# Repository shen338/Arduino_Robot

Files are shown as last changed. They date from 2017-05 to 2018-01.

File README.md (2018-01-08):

# Arduino Controlled Autonomous Robot for Ball Collection
In this project, we do the following things:  
· Employed Pixy Camera and image segmentation algorithm to locate the ball and container in real time  
· Wrote PID algorithm for the robot to track and follow the ball, programmed in Arduino IDE  
· Collaborated on the design and fabrication the robots powertrain, sensor and navigation hardware  

### Two demo ball tracking videos and our performance in final competition

[Final Competition](https://www.youtube.com/watch?v=fU1fNfBJTtA)   
[Ball Tracking Demo 1](https://www.youtube.com/watch?v=Wlfwm1OvA4c)  
[Ball Tracking Demo 2](https://www.youtube.com/watch?v=8-BpY_hJBjg)  

### Appearance of our robot: 
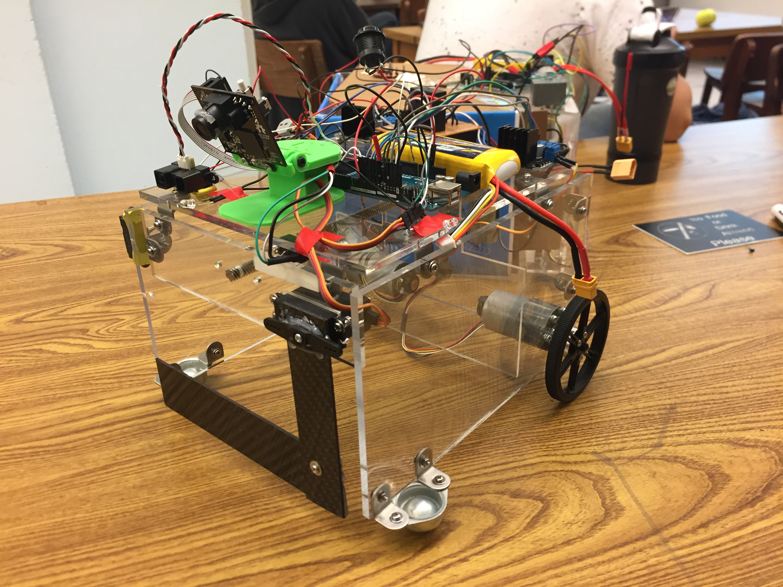
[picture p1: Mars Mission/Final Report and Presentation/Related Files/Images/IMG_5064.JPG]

### Appearance of our container: 
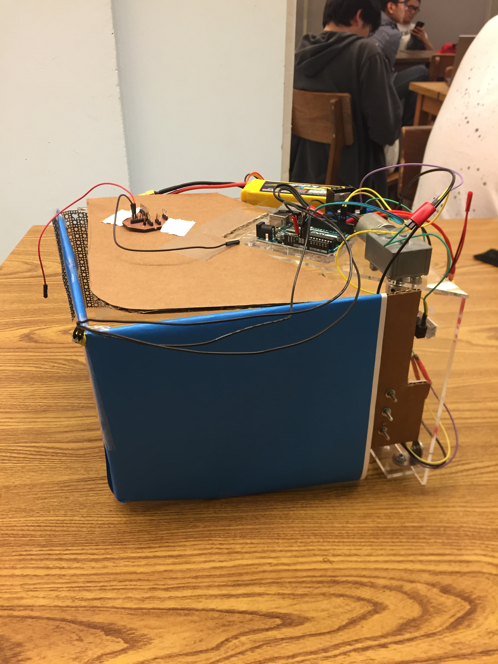
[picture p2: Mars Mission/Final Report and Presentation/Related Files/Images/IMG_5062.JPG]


#### All the source code is in the code/Master folder.

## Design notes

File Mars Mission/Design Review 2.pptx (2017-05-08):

## Design Review 2

Team 8
Ze An
Priyanka Anantha
De-Wei Chang
Andria Nyenhuis
Tong Shen

## FSM for the robot

Ball Tracking
TrackBlock(blocks,1);

size >= threshold

ball < 3

Ball Collecting
BallCollecting();

ball = 3

Ball Dispensing
BallPushing();

size >= threshold

Container Tracking
TrackBlock(blocks,2);

## FSM for ball dispensing

Forward
forward(255);

front switch = 0

Backward
backward(255);

rear switch = 0

Stop
backward(0);

## FSM for the container

Ball Tracking
TrackBlock(blocks,1);

size >= ?

ball < 3

Ball Collecting
BallCollecting();

ball = 3

Ball Dispensing
BallPushing();

Container Tracking
TrackBlock(blocks,2);

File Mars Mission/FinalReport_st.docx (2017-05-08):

1. ABSTRACT (Andria)
2. INTRODUCTION (Andria)
3. MECHANICAL SYSTEMS (Priyanka)
  3.1. Chassis and Component Mounts
  3.2. Trapdoor Mechanism
  3.3. Dispensing Mechanism
  3.4. Container
4. ELECTRONICS AND POWER SYSTEMS
  4.1. Microcontroller (De-Wei)

We used Arduino Mega 2560 as our controller on the robot because there are lots of pins on it to accommodate the pixy cam, three DC motors, a servo motor, two IR sensors, and infrared emitter. For the container, we use Arduino Uno as the controller due to just one DC motor and an infrared receiver.

  4.2. Actuators (De-Wei)
    4.2.1. Drive Motors

For the drive system, two 12V DC motors with encoders were used. These motor have no load speed of 251 rpm and 43.7:1 metal gearbox, which make it rotate fast and powerful. With L298N motor drive board, these motors can be easily controlled.

    4.2.2. Dispensing and Container Lead Screw Motor

For the lead screw driving motor, we used a 12V DC worm geared motor, which has huge torque to push heavy tennis balls. The only problem of this motor is that the rotational speed is not enough. Therefore, we couldn’t push the balls fast enough to have sufficient momentum to roll into the container by itself. As a result, we had no choice but to change the way we dispense the tennis balls.

    4.2.3. Trapdoor Motor

In order to easily control the door to be the specified positions, a servo motor was used to move the trapdoor. Moreover, there was no huge load on the door. Therefore, a servo motor was our best option.

  4.3. Sensors (Tong)
    4.3.1. Ball Detection

The ball detection mechanism is the core sensing part of our robot. Basically, we use the Pixy camera detection system to complete this part. First, we need to find the balls. To do this, we made our robot rotate itself if no ball was detected. And it also moved straight for a short distance in every 3 seconds to search in a different location. If a ball was detected, we need to detect the location of the ball as well as the distance between the ball and the vehicle. First, we need to know the relative position of the ball to navigate our vehicle. At very beginning, we used pan servo to rotate pixy to keep the ball in the center of the pixy camera and read the rotating angle of pan servo to compensate the move direction of our vehicle. In this way, we could successfully collect the ball but it was not fast enough and the precision and stability was not easy to control. So, we removed the pan servo and install the camera directly to our vehicle and read the relative position of the ball blocks in the image to compensate the moving direction of our vehicle. In this way, we could move our vehicle efficiently to the balls.

If the distance between the ball and the vehicle is small enough, we need to get into the collection state. First, we use the ball’s block size in the image to determine this distance. It turned out that the algorithm of the block size is unreliable in some corner cases. And then we found that y coordinate of the ball block in the image could also represent this distance. So, we changed our method and let the robot get into collection state after the ball block position in the image was low enough. In this way, we could make sure the vehicle would get into collection state every time at certain distance in front of the ball.

    4.3.2. Lead screw switches

To prevent the lead screw from moving beyond the limit to damage other components, we added to two switches in both side of the lead screw to regulate its moving range. Once the moving part touched the switch, it would stop or move to opposite direction immediately.

    4.3.3. Container Detection

It was easy to detect the container but the critical part was how to keep the alignment of the vehicle and the container to make sure the ball was dispensed in the right direction. We tested different method like the color code or mechanical structure guidance. But these method was not robust enough and couldn’t perfectly work in different situations. And then, we thought out of box and decided to change the shape of our container. We made a rectangle container and used a big color bar as a symbol. In this way, we didn’t need to worry about the vehicle direction in common cases. Our vehicle stopped in front of the container and got into dispensing state.

    4.3.4. Ultrasonic detection

In order to prevent our vehicle from hitting the wall, we introduced two ultrasonic sensor to our robot. In the searching mode, if any ultrasonic detected something, we could make some changes based on this information. We also developed an FSM for this to make sure our robot could go to the right way.

Task Completion - Container Door Close

For the door open and close, we used infrared signal as remote control to operate the container door. We installed three infrared emitter in the front and both sides of our robot and placed one receiver at the center of the container door. In this way, we could use our robot to open and close the container door.

  4.4. Power System
5. SOFTWARE (Ze An)
  5.1. Find Ball State
  5.2. Move to Ball State
  5.3. Obtain Ball State
  5.4. Dispense Ball State
  5.5. Container Close State
6. RESULTS
  6.1. Experiments and Testing
    6.1.1. Drive Motor Torque Testing (Ze)
    6.1.2. Ball Detection Testing (De Wei)

At the beginning, we used Pixy with pan and tilt servos mounted so that it can move as eyes on human's neck in order to get more vision. We first used the center point of the pixy camera to minus the x and y position of the block of the object to get the error, and use it to control the movement of the servo motors. After that, we took the angles the servos move from center as the error. With this error, we then built the differential speed for each sides of the motors to track the object. However, with feedback loop, it increased the difficulties to control the robot. As a result, we could successfully track tennis balls, but we failed to align with the balls perfectly. In other words, sometimes we might stop next to the ball, rather than in front of the ball, which made us unable to collect the ball. Therefore, we then tried to simplified the design and got rid of the pan and tilt servos, which sacrificed the broader range of vision. Without the servos for pan and tilt, we directly used the x axis error of pixy to build the differential speed for each motors. In this method, our robot would rotate without forward speed to search for the ball. Once aligned, it would go straight and collect it.

    6.1.3. Ball Collection Performance Testing (De Wei)

For the collection, we initially used size as the threshold to tell Arduino when to go into the collect state. However, after several tests, we found out that it was not stable as the size might vary with the light condition. Thus, we modified our method and used y position of the object as the threshold. We first used the serial monitor to find out the desired value as the robot approaching the tennis ball. After getting the desired value, we put it into the program and tested.

    6.1.4. Ball Dispensing Performance Testing (Andria)

The initial concept was to dispense the balls was to use a push plate driven by a lead screw mechanism. The plate however did not push the balls paste the plain of the vehicle. There were concerns that

    6.1.5. Container Door Performance Testing (Priyanka)
  6.2. Budget (Andria)
  6.3. Competition Performance (Andria)
7. DISCUSSION (Andria)
8. CONCLUSIONS (Andria)
9. REFERENCES
10. APPENDIX

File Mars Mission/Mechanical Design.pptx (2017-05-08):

## Mechanical Design

## Chasis

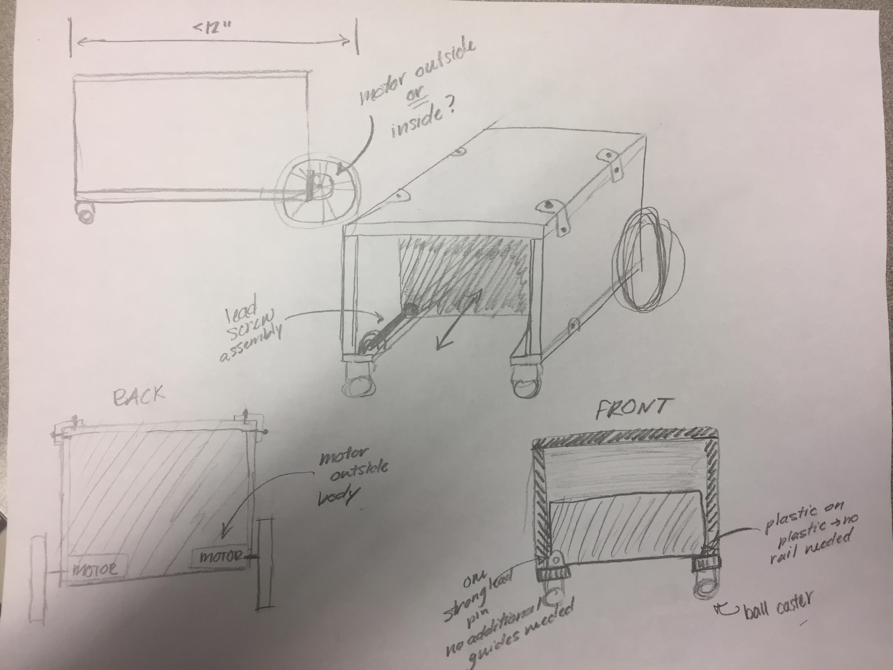
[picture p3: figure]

Andria’s concept

## BOM

ITEM | STATUS | LINK
Corner brackets | purchased | https://www.amazon.com/Tinksky-Stainless-Degree-Bracket-Fastener/dp/B01JOVO1N2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
M3 fasteners | purchased | https://www.amazon.com/290pcs-Phillips-Washers-Assortment-Stainless/dp/B01K6NNYZ8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
Lead screw assembly | purchased | https://www.amazon.com/Witbot-Pillow-Bearing-Coupler-Printer/dp/B01MXYIWTD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
3/4" Plastic Ball Caster | purchased | http://www.robotshop.com/en/pololu-ball-caster-3-4-in-plastic-ball.html

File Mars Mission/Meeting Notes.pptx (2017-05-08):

## Meeting Notes

Compiled

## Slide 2

Week | ACTIVITY 1 | ACTIVITY 2 | ACTIVITY 3 | ACTIVITY 4
2/27 | Prototype of body/chassis | Define motor req | Define container | Define sensor technology
3/6 | Define ball collector mechanism
3/13 (SPRING BREAK)
3/20 | Validate sensor technology
3/27
4/3 | 1st Design Critique
4/10
4/17 | 2nd Design Critique
4/24 | | | Report and Due day

## Meeting Notes

Friday, Feb 17

## Discussion

- Need to have rough idea of prototype by spring break to begin ordering parts
- Meet 2x a week until spring break
  - Tuesday 7 PM - weekly
  - Thursday 7 PM - weekly
  - Possibly additional meeting (March 3rd I think it was??)
- Image processing is slow
  - Not accurate
  - Not robust to different lighting
- Infrared could be a good option
- Ultra sonic would be difficult with walls reflecting
- possibly split team into subsystems : mechanical and electrical
- Corral the balls versus pick them up
- Compartment door could be passive by having it swivel on a hinge

## Product Attributes

- Robot
  - Drive motor/gears
  - Chassis
    - Wheels
    - Axles
  - Collecting system
    - Drive
    - Mechanism
  - Sensors
    - Detect wall
    - Detect ball
    - Detect compartment
  - Decorations
  - Body
  - Control board
  - Battery

- Compartment (12”x10”x6”)
  - Door (8”x6”)
    - Lift mechanism
    - Lift drive
      - Control board
      - Battery
  - Walls
  - Sensors
  - Decoration
    - Lighting
- Transportation Carrier (12”x12”x12”)

## Alumni Discussion

Feb 22, 2017

## Alumni meet discussions

Points noted:
- Options for sensing the balls:
  - IR sensors (noise and rangle problems)
  - Ultrasonic (noise problems)
  - Image sensors (pixy- compatible with raspberry pi, slow and takes more processing time but easier bot manipulation)
- To detect and align with container:
  - Hall effect sensor (short range distance)
  - Beacon (light emitting/wireless) (wireless-complicated)
- Use limit switches to detect collision with walls and helping in repositioning bot
- Can use encoders for position calculations but very tough to retrace steps
- Choose good friction tyres to avoid slip
- Brake/reverse motors if we want to push the balls out
- Design top loading container as it can be placed in any orientation

## Meeting Notes

Feb 23, 2017

## Discussion

- Container can be placed in any orientation in any corner therefore it might be necessary to drop balls in from the top or have doors on every side
  - Discussed how a claw armature would be easiest for dropping ball into the top of container
  - Discussed a possible container that raises from the middle so can be accessed from all sides, rubber band “arena” would keep balls from escaping from container
- Pixy (https://www.youtube.com/watch?v=MN-jYF7WYY4) discussed as a possible way of finding balls.. $70+$40
- 3 wheels for vehicle (2 drive, 1 caster)
- Motors : DC or Step
  - Have code for each

- Need to have a weekly 1.5 hour meeting set - Monday’s are preference since ordering days are Tuesday and Thursday
- Timeline
  - Before spring break
    - Define container
    - Rough prototype of vehicle
      - Motors
      - Ball carrying method
- To Do: Research motors *must order by 2/29
  - Possible option Nema 17 bipolar step motor 3.5V

## Meeting Notes

Feb 27, 2017

## Discussion

- Motor
  - Still trying to determine if DC or Step motor is the best solution - decided to test both - senior design lab has several different motors we could use if we have a driver
- Decided not to spend our time designing for balls in the corner, if there is time near the end of the project we can implement a method for getting balls that are in the corner
- RPM
  - Determined that 2.5m/3s (0.83m/s) is fast
    - With a 10 cm diameter wheel, vehicle RPM 158, motor RPM 5283.9
    - Motor rated 5000 step/s = 1500 RPM
- Wheels should be 10 cm

- Meet Thursday at 8 PM
  - Test motors
  - Andria to bring body prototype materials

## 1st Order Request (2/28)

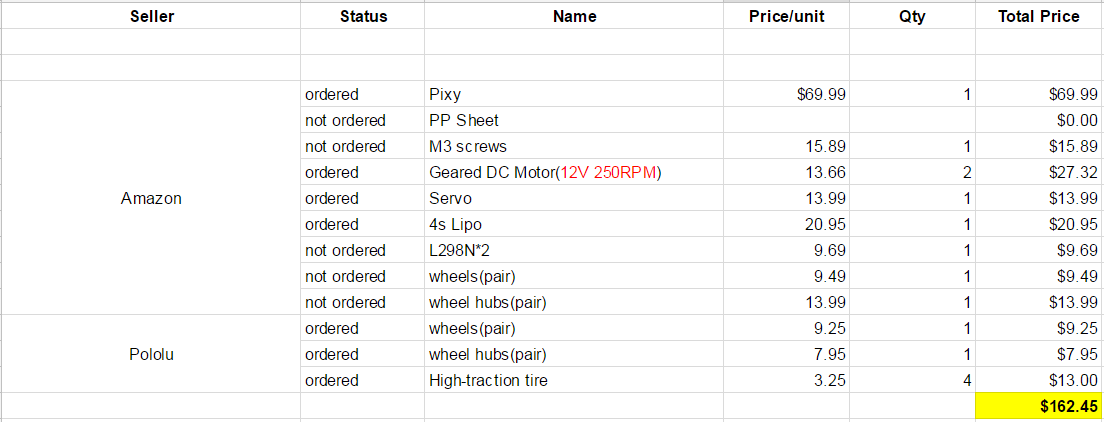
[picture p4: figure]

## Meeting Notes

March 2, 2017

## Discussion

- Andria’s friend asked prof/TA about balls being near the wall, they said they will not be placed near the wall.. They did not indicate the distance from the wall that would be considered “fair”
- Went through items we received for free from cabinets
  - See inventory sheet in folder
  - GB37Y3530-43 8EN DC Motor had great torque and RPM
  - Discussed if we should use the DC motors we order with worm gears or use GB37Y3530-43 8EN
- GB37Y3530-43 8EN would require the team to consider rear wheel drive and two front casters so that the front can remain open to capture balls - could keep motors in the front a create a “funnel” but we would be worried that the balls would reflect off of the funnel and not go through the funnel (see next slide for “funnel” concept
- Need to decide as a team if rear wheel drive would be okay? - this would require 2 front caster wheels.. Would casters mean too much start force? NEED TO DECIDE ASAP SO WE CAN ORDER!

- Built a container prototype
  - Decided it would be more simple to just have 2 doors (unless elastic band concept works)
    - Could use LED lights or color to lead robot to the correct door
  - Found that high ball force is required to push through the “flap” door
  - Considered strips of material.. Decided that would be a “curtain” not a door
  - May need to consider an axle type flap door so there is less force required to rotate (see next slide for axle flap door)
  - Did not try Ze’s elastic design but have elastic to try next time
  - Might need to consider a raising door if we can not get prototype to work

## Concepts

Front Wheel Drive Ball “Funnel”

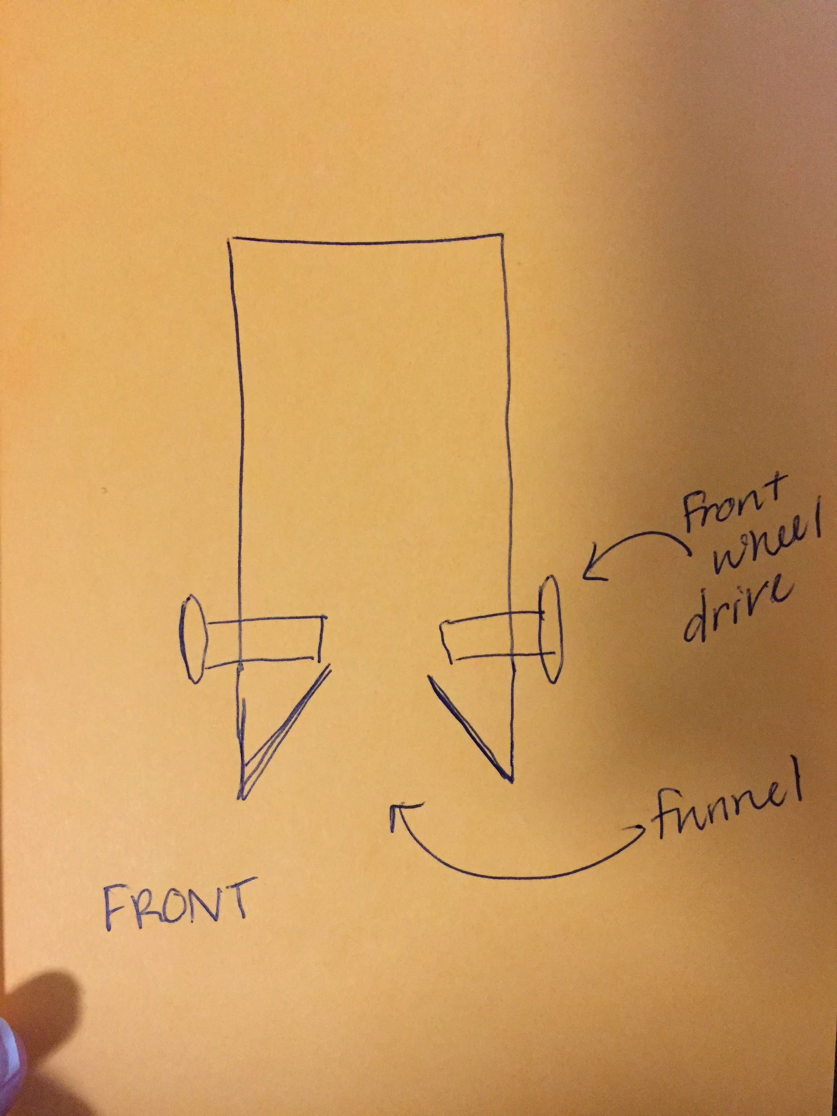
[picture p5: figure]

Axle Flap Door

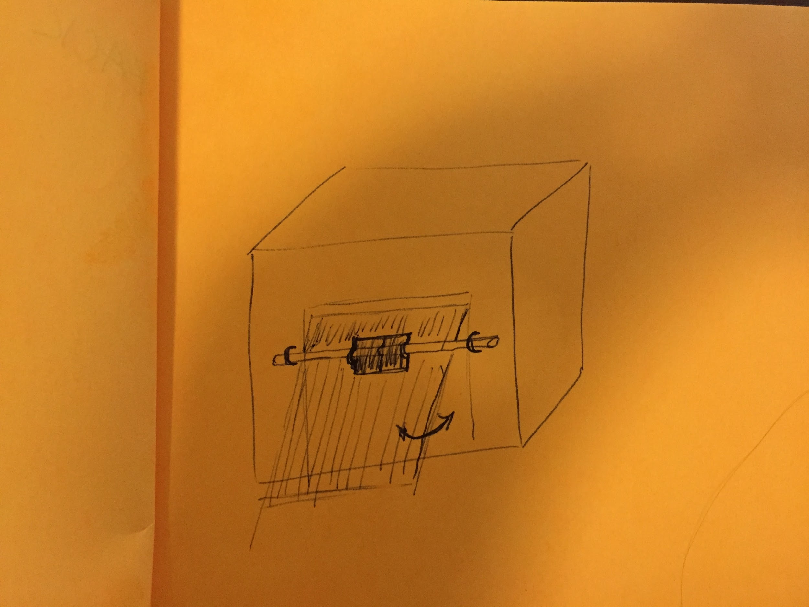
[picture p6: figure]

## Container Prototype

- Pros:
  - Easy to build
- Cons:
  - Requires a lot of force on the ball to push through doors

## Vehicle Prototype

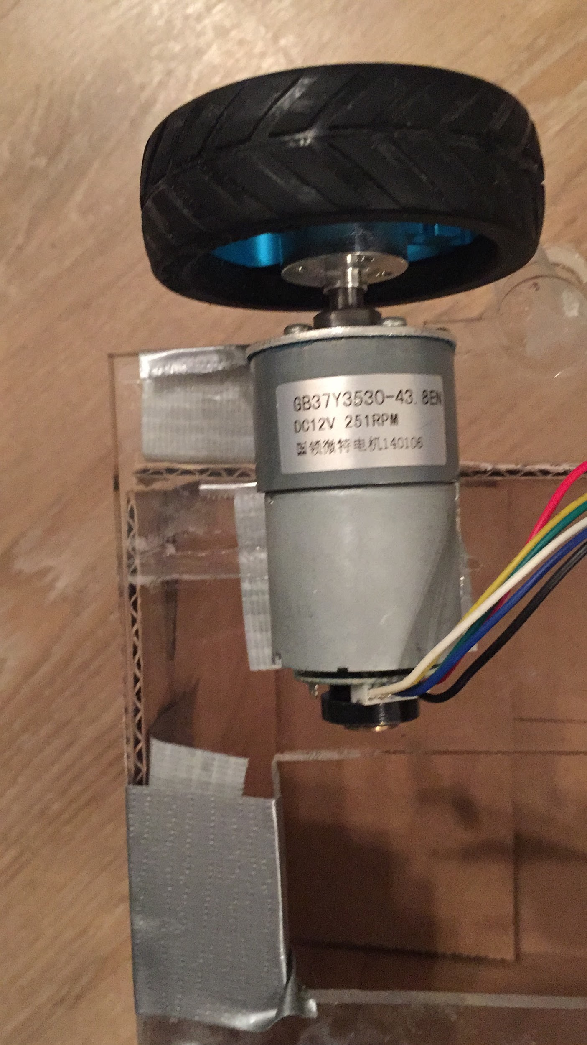
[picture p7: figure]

- 10”x7”x7”
- GB37Y3530-43 8EN
- 2.5” wheel

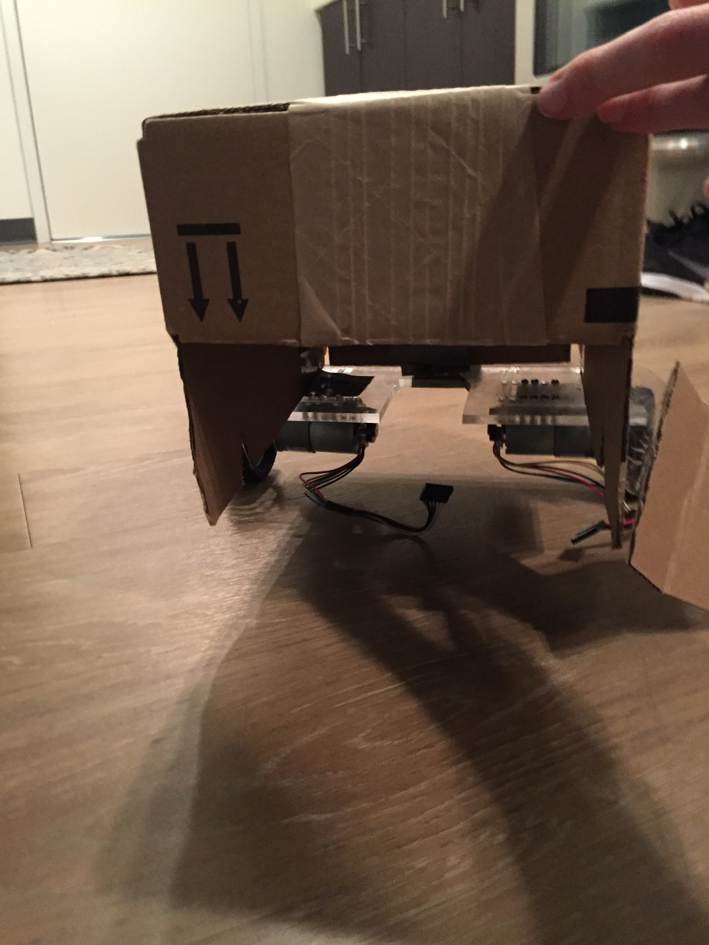
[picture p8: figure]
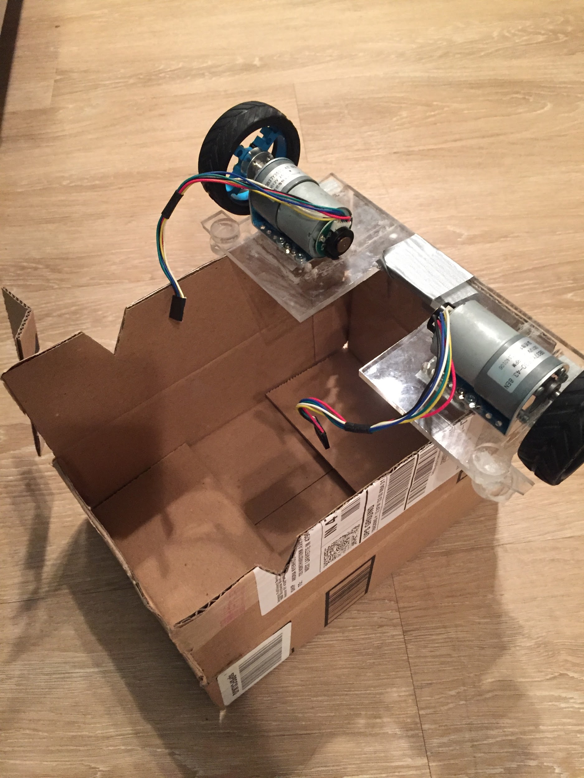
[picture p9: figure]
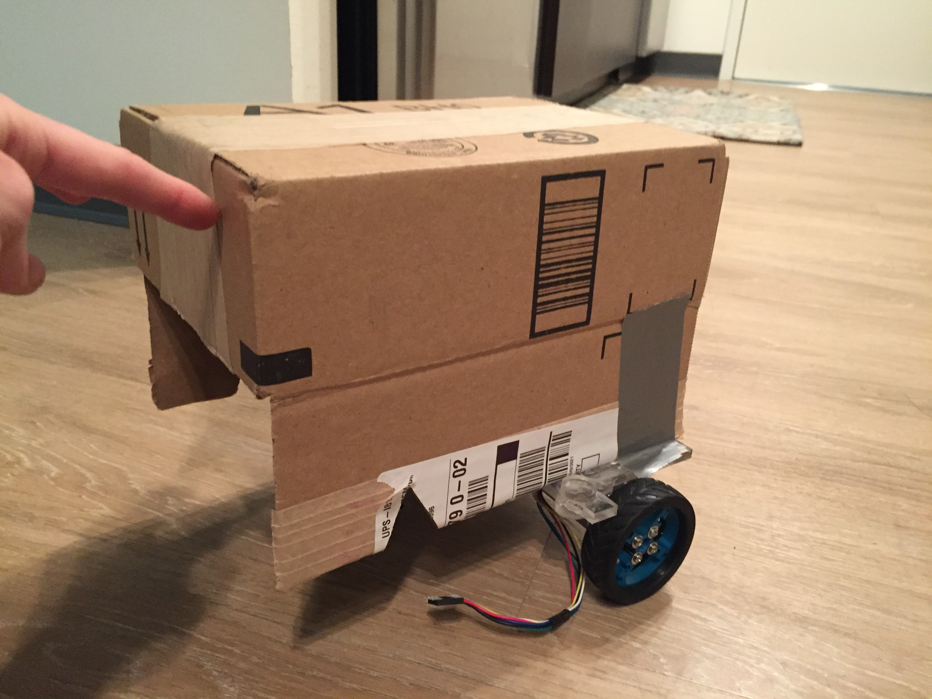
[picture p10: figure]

## Questions to ask in class

- Where to source our PCB through
- Door dimensions
- Door close time

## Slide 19

https://cdn-learn.adafruit.com/downloads/pdf/pixy-pet-robot-color-vision-follower-using-pixycam.pdf
https://create.arduino.cc/projecthub/junejarohan/ball-tracking-robot-7a9865
http://www.instructables.com/id/Pixybot-robots/?ALLSTEPS

## GitHub repository

https://github.com/MrBanana211/Mars_Mission

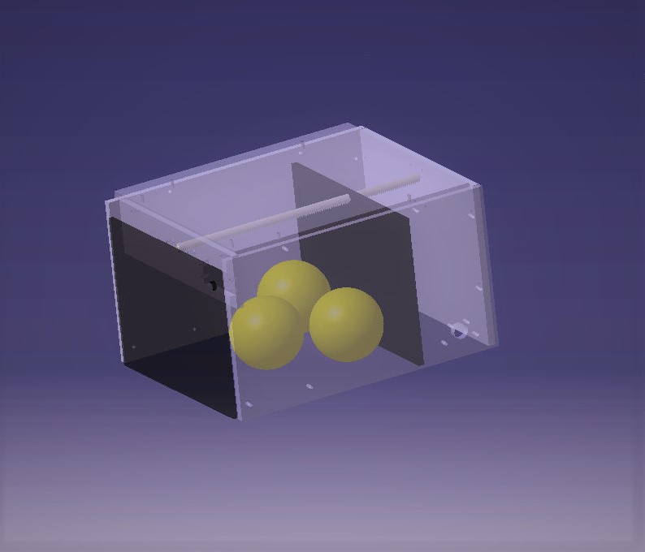
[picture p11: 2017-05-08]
Mars Mission/chassisdoor2.jpg

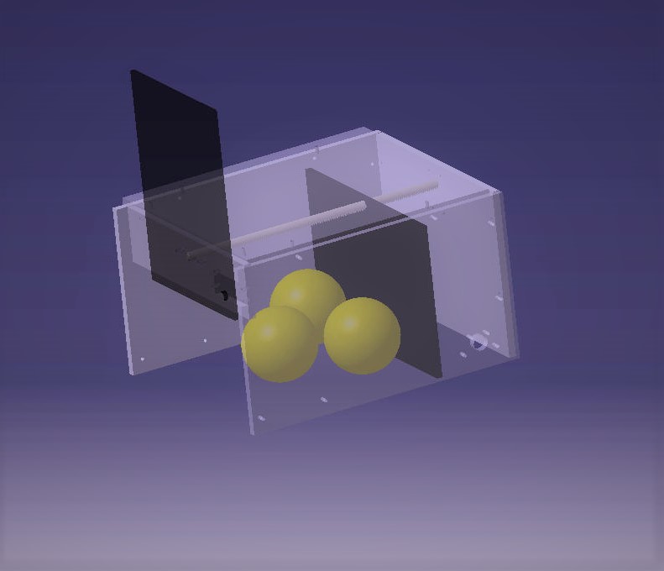
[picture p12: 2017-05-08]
Mars Mission/chassisdoor1.jpg

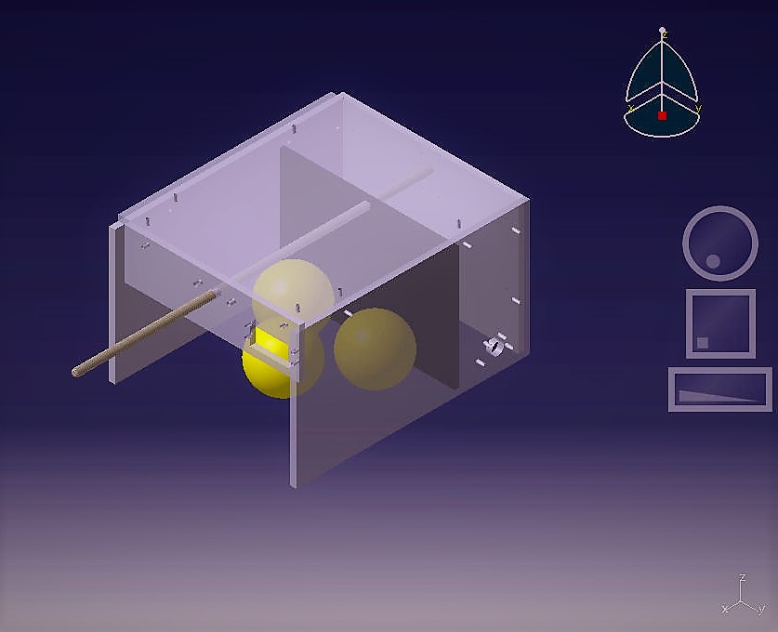
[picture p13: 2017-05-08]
Mars Mission/chassis1.jpg

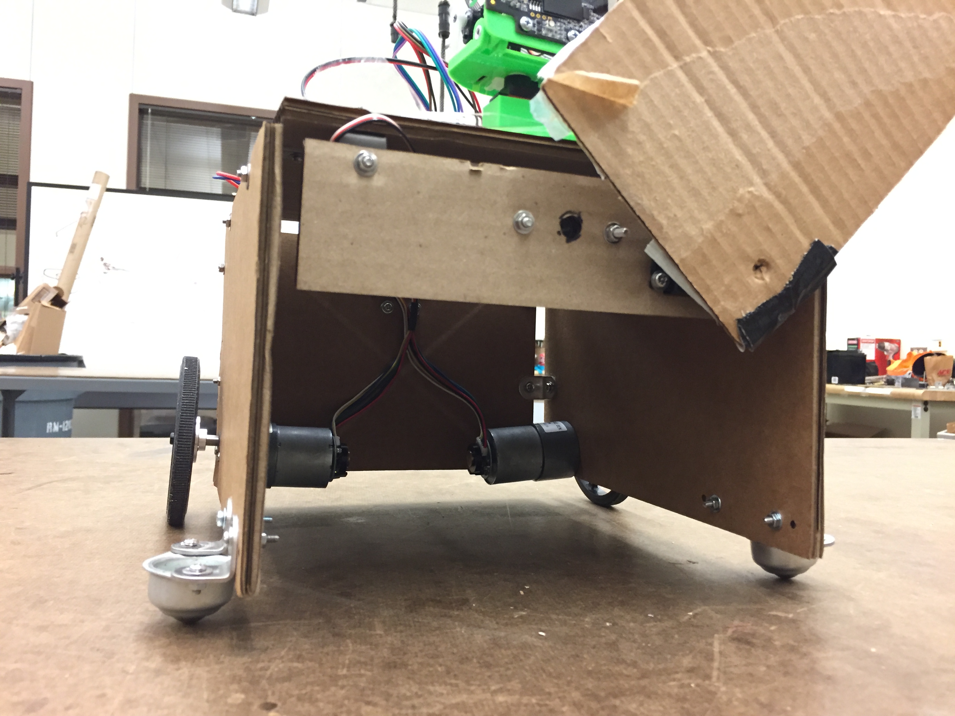
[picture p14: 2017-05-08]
Photos/2017-04-05 20.41.26.jpg

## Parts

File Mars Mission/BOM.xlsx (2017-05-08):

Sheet: Sheet1
Part Description | Subsystem | Vendor | Unit Price | Qty | Total Cost
Pixy Smart Vision | robot | amazon | 69.99 | 1 | 69.99
Geared DC Motor (12V 250 RPM) | robot/container | amazon | 13.66 | 2 | 27.32
Servo | robot | amazon | 13.99 | 1 | 13.99
wheels(pair) | robot | pololu | 9.25 | 1 | 9.25
wheel hubs (pair) | robot | pololu | 7.49 | 1 | 7.49
high traction tire | robot | pololu | 3.25 | 4 | 13
Ball Casters | robot | robot shop | 3.99 | 2 | 7.98
Witbot 400mm 8mm T8 Lead Screw Set | robot | amazon | 13.98 | 1 | 13.98
Corner Brackets | robot/container | amazon | 6.99 | 1 | 6.99
290pcs M3 Phillips Pan Head Fastener Assortment Kit | robot/container | amazon | 11.99 | 1 | 11.99
uxcell 6mm to 8mm Shaft Coupling | container | Amazon | 6.55 | 1 | 6.55
Hinge Roller Lever Micro Switches - 3 Pins 10 Pcs | robot/container | Amazon | 5.99 | 1 | 5.99
GB37Y3530-43 8EN | robot | on-hand | unknown | 2 | N/A
Arduino uno | container | on-hand | 24.95 | 1 | 24.95
Arduino Mega | robot | on-hand | 45.95 | 1 | 45.95
L298N | robot | on-hand | 3.23 | 3 | 9.69
ZIPPY Compact 1500mAh 3S 35C Lipo Pack | robot/container | on-hand | 14.34 | 2 | 28.68
Pixy servo | robot | on-hand | unknown | 1 | N/A
Pixy mount and servo | robot | on-hand | N/A | 1 | N/A
PCB | container | PCB Mill Shop | N/A | 1 | N/A
1/4" - 22"x18" arcylic sheet | robot | Menards | 19.94 | 1 | 19.94
1/8" - 22"x18" arcylic sheet | robot/container | on-hand | 16.48 | 1 | 16.48
5V voltage regualtor | robot | on-hand | unknown | 1 | N/A
Emergency switch | robot | on-hand | unknown | 1 | N/A
8 mm lead screw | container | on-hand | unknown | 1 | N/A
IR sensors (Qty:3) | robot/container | on-hand | unknown
LED (Qty 3) | robot | on-hand | unknown
carbon fiber scraps | robot | on-hand | unknown | 1 | N/A
TOTAL |  |  |  |  | 340.21

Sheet: Sheet2
Andria Out of Pocket Expenses
$25 | fasteners from Fastna
$40 | acrylic from menards (qty2)
$10 | L298N (Qty2)
$75 | SUM

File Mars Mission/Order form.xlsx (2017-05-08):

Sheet: Order 1
Seller | Status | Name | Price/unit | Qty | Total Price | Recieved status | Note | Link
Amazon | ordered | Pixy | $69.99 | 1 | $69.99 | Yes |  | https://www.amazon.com/Pixy-CMUcam5-Smart-Vision-Sensor/dp/B00IUYUA80
 | not ordered | PP Sheet |  |  | $0.00 |  | make cardboard prototype
 | not ordered | M3 screws | 15.89 | 1 | $15.89 |  |  | https://www.amazon.com/Hilitchi-210pcs-Stainless-Socket-Assortment/dp/B014ONCP88
 | ordered | Geared DC Motor(12V 250RPM) | 13.66 | 2 | $27.32 |  | Choose the one wiht Prime | https://www.amazon.com/dp/B01N990WOU/ref=olp_product_details?_encoding=UTF8&me=
 | ordered | Servo | 13.99 | 1 | $13.99 | Yes |  | https://www.amazon.com/Parallax-Inc-Continuous-Rotation-Servo/dp/B00B886KSE
 | ordered | 4s Lipo | 20.95 | 1 | $20.95 |  | 1300mAh | https://www.amazon.com/gp/product/B013I9RLVK/ref=ox_sc_act_title_2?ie=UTF8&psc=1&smid=A3T39NG71SCCQP
 | not ordered | L298N*2 | 9.69 | 1 | $9.69 |  |  | https://www.amazon.com/Stepper-Controller-Mega2560-Duemilanove-IFANCY-TECH/dp/B01GZ1QUHO?s=hi
 | not ordered | wheels(pair) | 9.49 | 1 | $9.49 |  | If possible buy from Pololu | https://www.amazon.com/gp/product/B00T3MQEU6/ref=ox_sc_act_title_1?ie=UTF8&psc=1&smid=A2XU70B31JRNMP
 | not ordered | wheel hubs(pair) | 13.99 | 1 | $13.99 |  | If possible buy from Pololu | https://www.amazon.com/Pololu-UNIVERSAL-ALUMINUM-MOUNTING-SHAFT/dp/B00B887FX8
Pololu | ordered | wheels(pair) | 9.25 | 1 | $9.25 | Yes |  | https://www.pololu.com/product/1431
 | ordered | wheel hubs(pair) | 7.95 | 1 | $7.95 | No |  | https://www.pololu.com/product/1083
 | ordered | High-traction tire | 3.25 | 4 | $13.00 | Yes | We definitely want these | https://www.pololu.com/product/694
 |  |  |  |  | $162.45

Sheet: Order 3
Seller | Name | Price/unit | Quantity | Total price | Link
Amazon | 6 mm to 8mm Helical Coupler | 6.99 | 1 | 6.99 | https://www.amazon.com/uxcell-5mmx8mm-Helical-Coupler-Coupling/dp/B06X99P2XK
 | uxcell 2 Pcs KFL08 8mm Zinc-Aluminum Alloy Flange Pillow Block Bearing | 9.15 | 1 | 9.15 | https://www.amazon.com/uxcell-Zinc-Aluminum-Flange-Pillow-Bearing/dp/B00N4138LU
 | uxcell 6mm to 8mm Shaft Coupling 25mm Length 18mm Diameter Stepper Motor Coupler Aluminum Alloy Joint Connector for 3D Printer CNC Machine DIY Encoder

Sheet: Order 2
Name | Price/unit | Quantity | Total price | Link
Pololu Ball Caster with 3/4" Plastic Ball | 3.99 | 2 | 7.98 | http://www.robotshop.com/en/pololu-ball-caster-3-4-in-plastic-ball.html
Witbot 400mm 8mm T8 Lead Screw Set Lead Screw+ Pillow Bearing Block + Copper Nut + Coupler for 3D Printer | 13.98 | 1 | 13.98 | https://www.amazon.com/Witbot-Pillow-Bearing-Coupler-Printer/dp/B01MXYIWTD
corner brackets | 6.99 | 1 | 6.99 | https://www.amazon.com/Tinksky-Stainless-Degree-Bracket-Fastener/dp/B01JOVO1N2?rps=1
290pcs M3 Phillips Pan Head Screws Bolts Nuts Lock Flat Washers Assortment Kit (M3,304 Stainless Steel) | 11.99 | 1 | 11.99 | https://www.amazon.com/290pcs-Phillips-Washers-Assortment-Stainless/dp/B01K6NNYZ8
 |  |  | 40.94
 | all received in Order 2

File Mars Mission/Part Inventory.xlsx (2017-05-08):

Description | Model Number | Picture | Notes
2 DC motors with 2.5" wheels | GB37Y3530-43 8EN |  | with encoders, and mounting base | https://www.dfrobot.com/wiki/index.php/12V_DC_Motor_251rpm_w/Encoder_(SKU:_FIT0186)
elastic band
variety of resistors
four bar link mechanism
2 Arduino Mega's |  |  | not sure if they work
2 heavy duty 2.5" casters
2 stepper motors with 2.75" wheels | 42BYGHM809
2 DC motors 3.5" wheels | LT25GA75-370T |  | 6V, 155+/- PRM, 1:75 gear ratio
gears and fasteners
11.1V 5000mAh 3-cell LiPo battery | TP5000-3sPP65
2* 2.5KG Electromagnet DC 12V P20/15 Holding Electric Magnet Lifting Solenoid |  |  | http://www.ebay.com/itm/like/162408602021?lpid=82&chn=ps&ul_noapp=true
breadboard
3* ultrasonic sensor | HC-SR04
2* bluetooth module
fuse
Dual MC33926 Motor Driver Carrier |  |  | https://www.pololu.com/product/1213
AC/DC power supply | LM2577 |  | https://www.amazon.com/Universal-adjustable-Module-Regulator-Booster/dp/B0043BHBR2
2* OP Amp | LM741
2* 8-bit ADC | ADC0809CCN |  | http://www.ti.com/lit/ds/symlink/adc0809-n.pdf
ISD 1420P

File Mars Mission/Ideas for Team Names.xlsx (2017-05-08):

Name | Reference
Ares | greek god of war

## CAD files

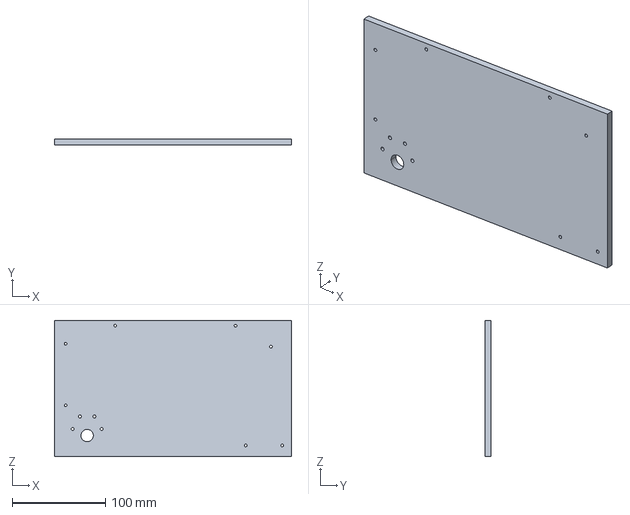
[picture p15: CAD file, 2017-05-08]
Mars Mission/Final Report and Presentation/Related Files/CAD Files/STP parts_chassis/sidewall.stp
254.0 x 6.35 x 146.1 mm

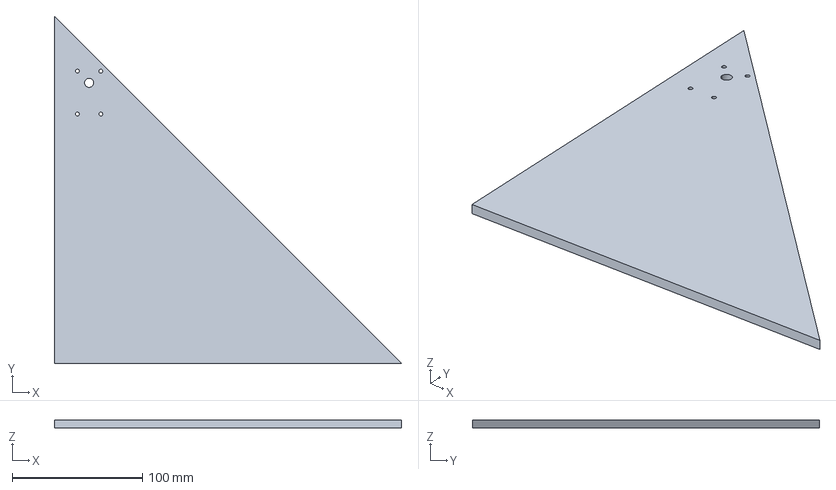
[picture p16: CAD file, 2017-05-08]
Mars Mission/Final Report and Presentation/Related Files/CAD Files/STP parts_container/top.stp
266.7 x 266.7 x 6.35 mm

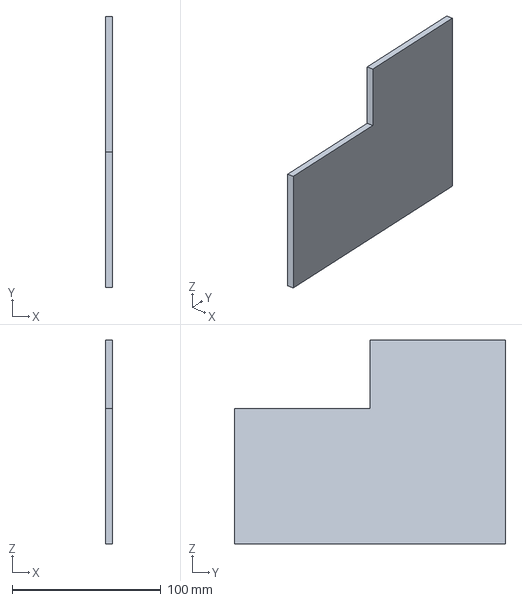
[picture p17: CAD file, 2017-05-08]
Mars Mission/Final Report and Presentation/Related Files/CAD Files/STP parts_chassis/door1.stp
5.00 x 182.5 x 137.1 mm

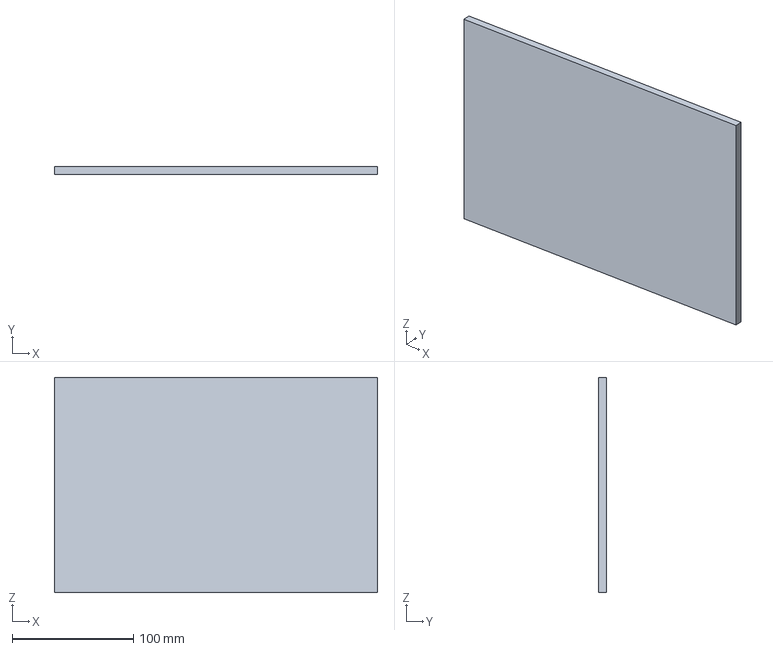
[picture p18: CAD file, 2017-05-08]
Mars Mission/Final Report and Presentation/Related Files/CAD Files/STP parts_container/c_wall.stp
266.7 x 6.35 x 177.8 mm

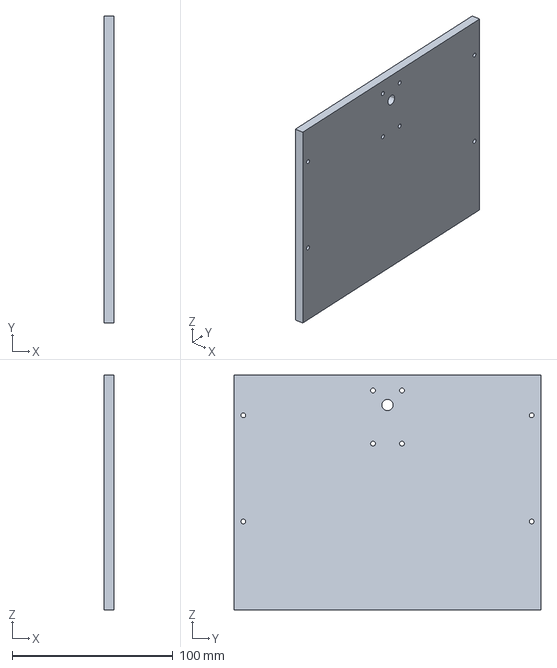
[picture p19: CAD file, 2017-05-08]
Mars Mission/Final Report and Presentation/Related Files/CAD Files/STP parts_chassis/backwall.stp
6.35 x 190.5 x 146.1 mm

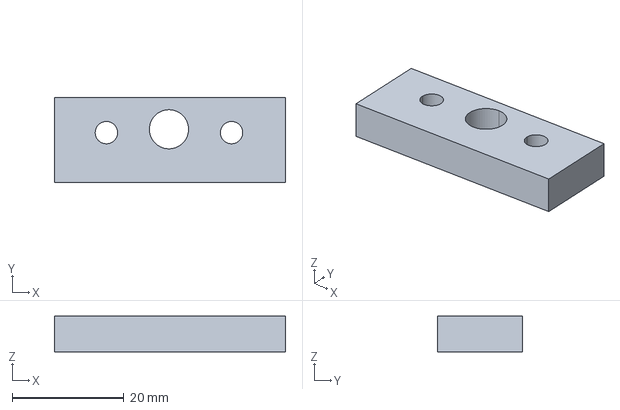
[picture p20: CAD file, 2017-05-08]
Mars Mission/Final Report and Presentation/Related Files/CAD Files/STP parts_container/support.stp
41.3 x 15.2 x 6.35 mm

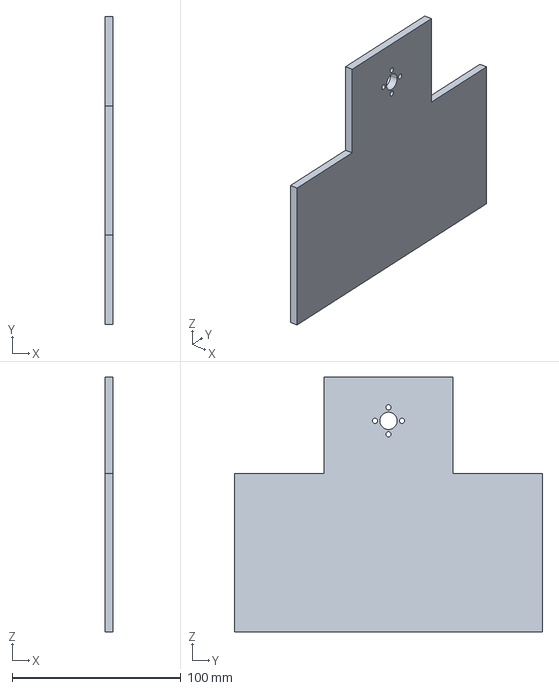
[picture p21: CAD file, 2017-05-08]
Mars Mission/Final Report and Presentation/Related Files/CAD Files/STP parts_chassis/plate.stp
5.00 x 183.0 x 151.3 mm

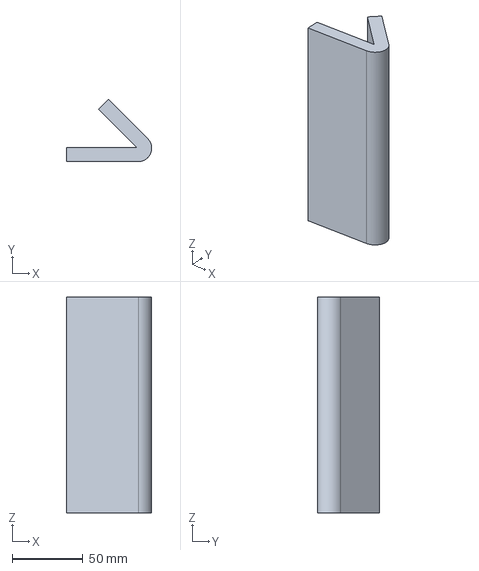
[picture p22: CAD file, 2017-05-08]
Mars Mission/Final Report and Presentation/Related Files/CAD Files/STP parts_container/guide.stp
60.3 x 44.0 x 152.4 mm

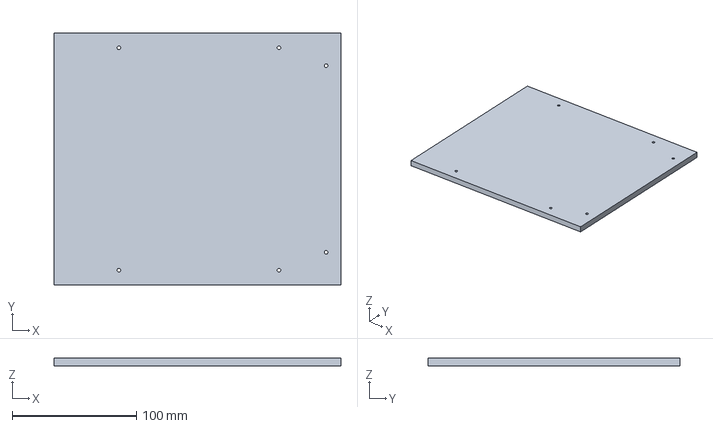
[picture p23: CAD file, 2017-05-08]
Mars Mission/Final Report and Presentation/Related Files/CAD Files/STP parts_chassis/topwall.stp
231.3 x 203.2 x 6.35 mm

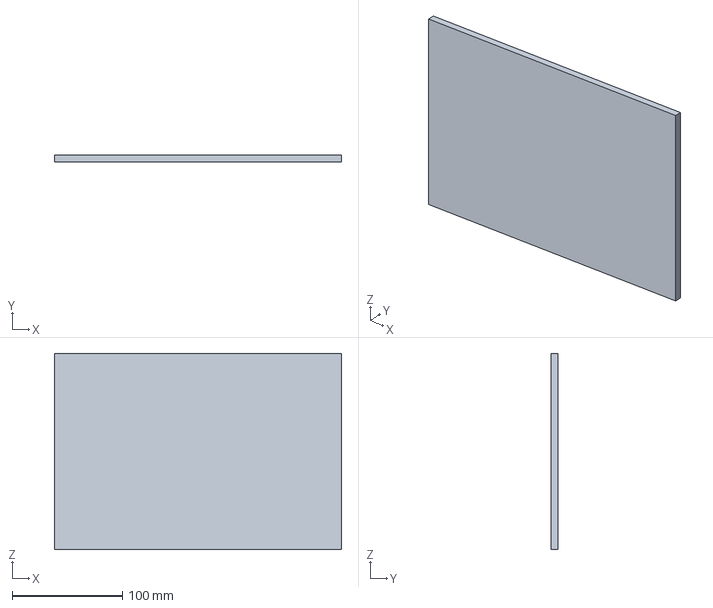
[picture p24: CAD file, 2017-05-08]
Mars Mission/Final Report and Presentation/Related Files/CAD Files/STP parts_container/c_wall2.stp
260.4 x 6.35 x 177.8 mm

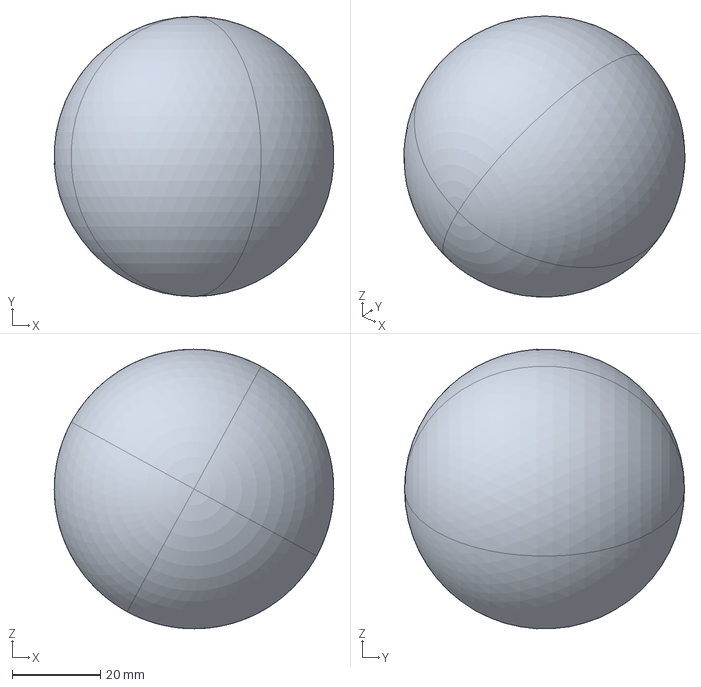
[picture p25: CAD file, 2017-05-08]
Mars Mission/Final Report and Presentation/Related Files/CAD Files/STP parts_chassis/balls.stp
63.4 x 63.5 x 63.4 mm

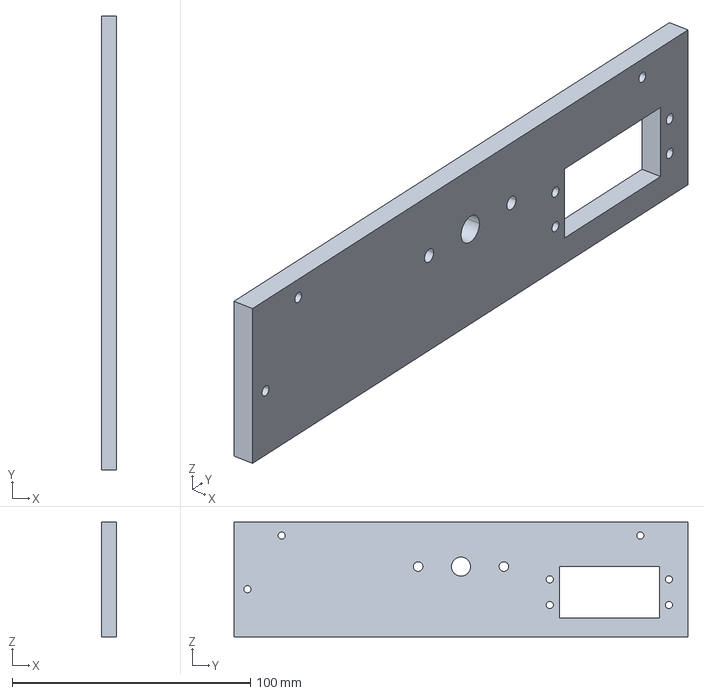
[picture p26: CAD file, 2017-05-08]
Mars Mission/Final Report and Presentation/Related Files/CAD Files/STP parts_chassis/frontwall.stp
6.35 x 190.5 x 48.2 mm

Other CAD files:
Mars Mission/Final Report and Presentation/Related Files/CAD Files/chassis2.dwg
Mars Mission/Final Report and Presentation/Related Files/CAD Files/Drawing1.dwg

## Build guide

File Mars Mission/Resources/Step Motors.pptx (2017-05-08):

## Step Motors

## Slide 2

https://www.youtube.com/watch?v=bkqoKWP4Oy4
http://www.servomagazine.com/index.php/magazine/article/september2014_Wierenga

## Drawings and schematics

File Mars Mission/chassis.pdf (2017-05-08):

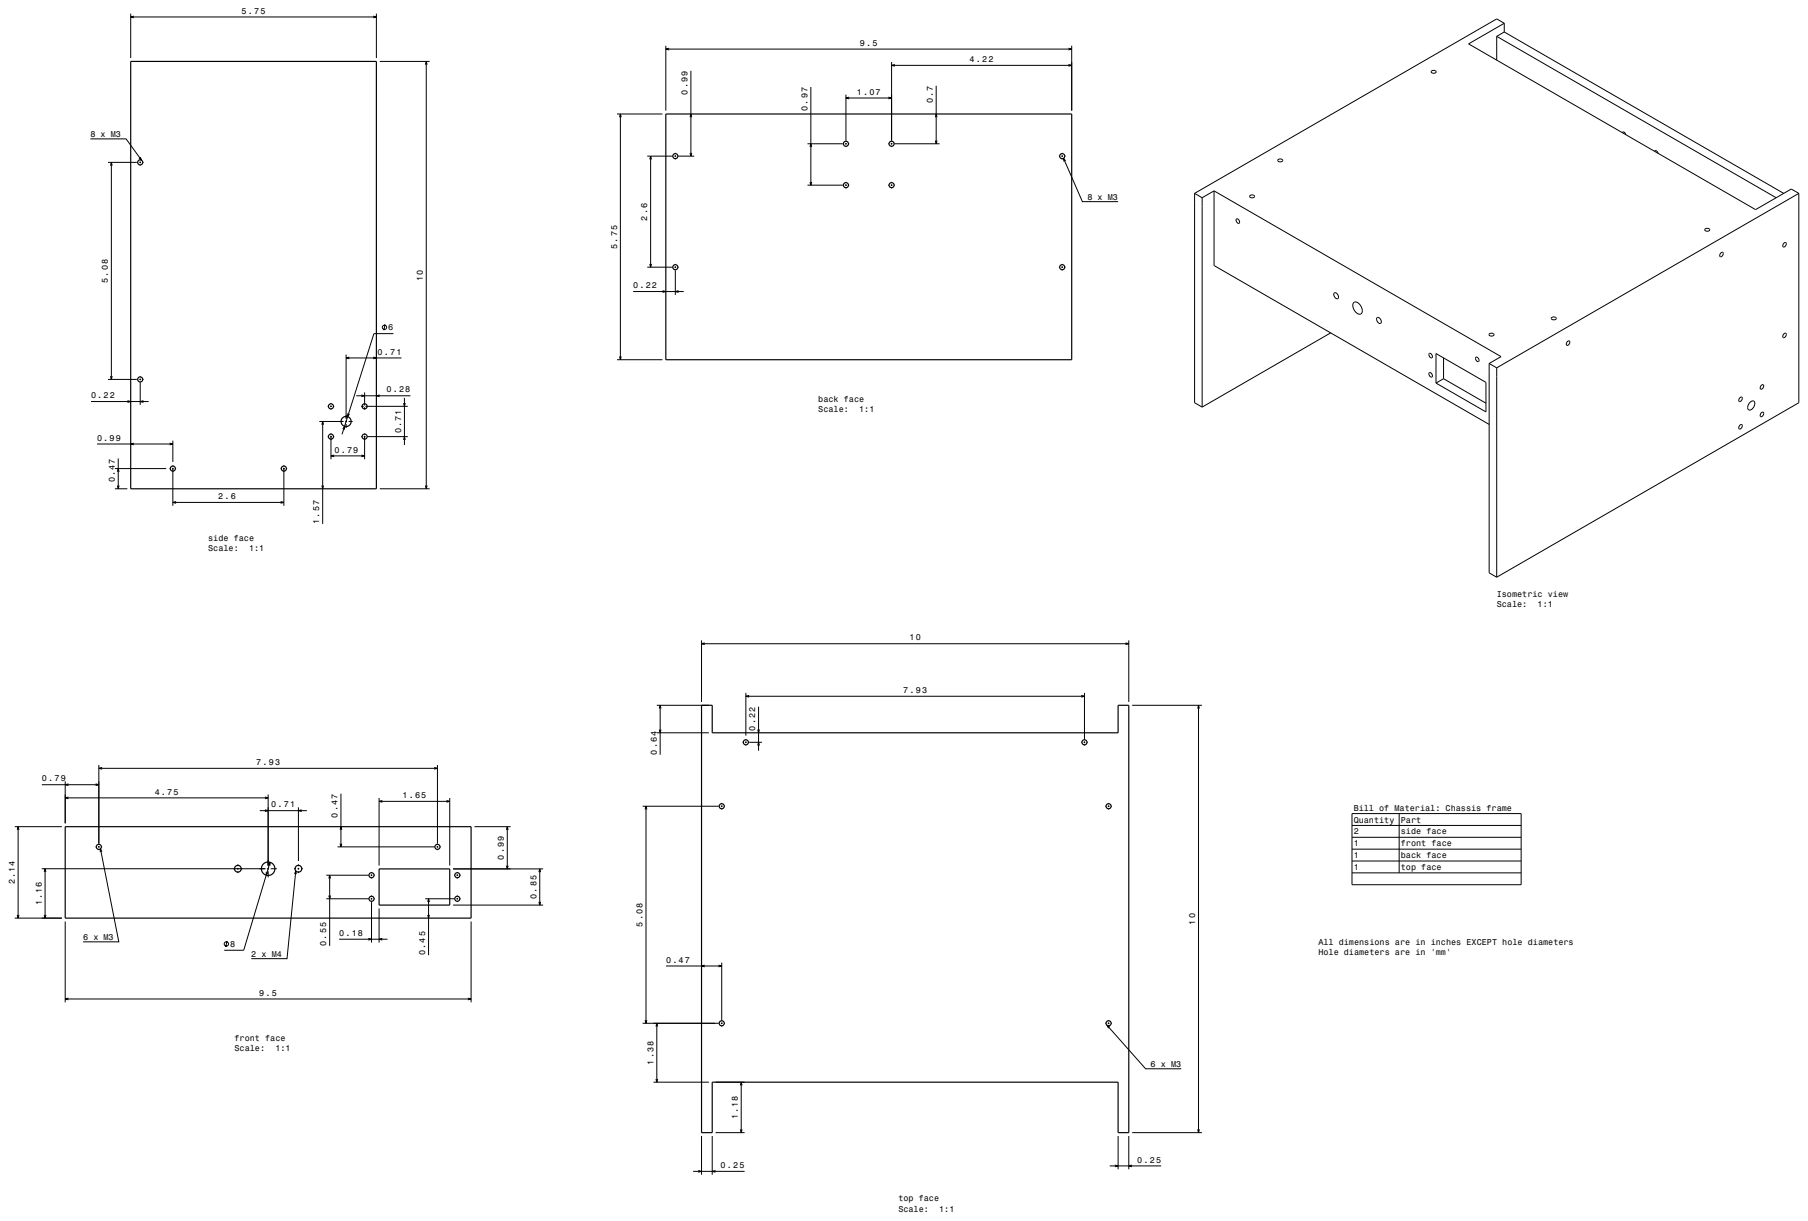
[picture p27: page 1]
side face Scale: 1:1; back face Scale: 1:1; top face Scale: 1:1; front face Scale: 1:1; Isometric view Scale: 1:1

Bill of Material: Chassis frame

Quantity | Part
2 | side face
1 | front face
1 | back face
1 | top face

All dimensions are in inches EXCEPT hole diameters
Hole diameters are in 'mm'

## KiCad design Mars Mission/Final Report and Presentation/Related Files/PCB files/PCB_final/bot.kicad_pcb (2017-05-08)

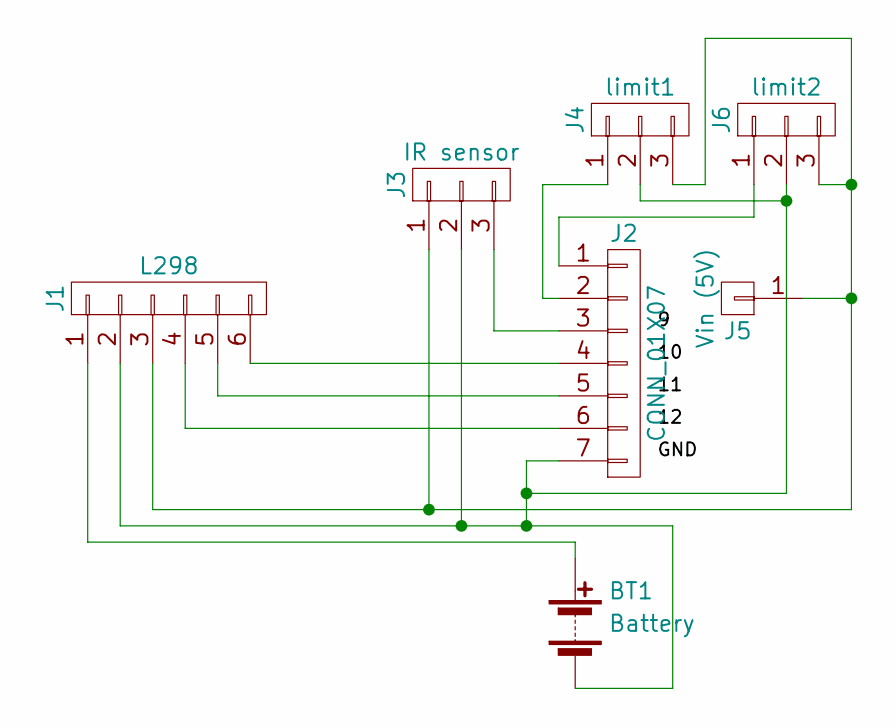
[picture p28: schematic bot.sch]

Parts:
BT1: Battery; Pin_Header_Straight_2x01_Pitch2.54mm
J1: L298; Pin_Header_Straight_1x06_Pitch2.54mm
J2: CONN_01X07; Pin_Header_Straight_1x07_Pitch2.54mm
J3: IR sensor; Pin_Header_Straight_1x03_Pitch2.54mm
J4: limit1; Pin_Header_Straight_1x03_Pitch2.54mm
J5: Vin (5V); Pin_Header_Straight_1x01_Pitch2.54mm
J6: limit2; Pin_Header_Straight_1x03_Pitch2.54mm

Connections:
unnamed: BT1.1 (+), J1.1
unnamed: BT1.2 (-), J1.2, J2.7, J3.2, J4.2, J6.2
unnamed: J1.3, J3.1, J4.3, J5.1, J6.3
unnamed: J1.4, J2.6
unnamed: J1.5, J2.5
unnamed: J1.6, J2.4
unnamed: J2.1, J6.1
unnamed: J2.2, J4.1
unnamed: J2.3, J3.3

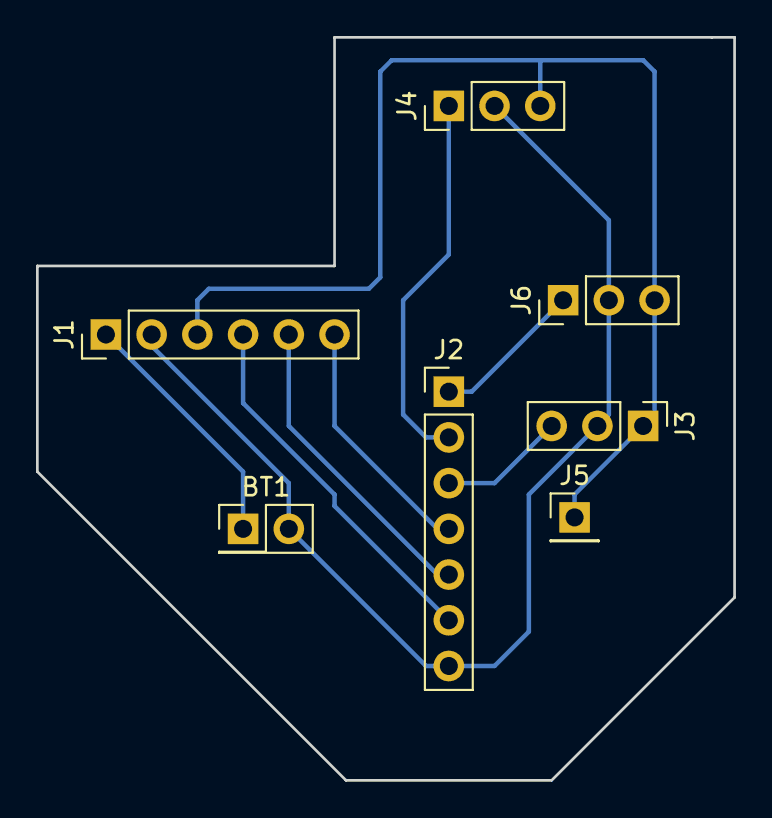
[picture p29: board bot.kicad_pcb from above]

Board: 2 copper layers, 38.7 x 41.3 mm, 7 parts (0 on the bottom side), 9 nets.

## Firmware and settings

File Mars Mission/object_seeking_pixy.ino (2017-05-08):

#include <SPI.h>
#include <Pixy.h>
//#include <ZumoMotors.h>
#define X_CENTER 160L
#define Y_CENTER 100L
#define RCS_MIN_POS 0L
#define RCS_MAX_POS 1000L
#define RCS_CENTER_POS ((RCS_MAX_POS-RCS_MIN_POS)/2)

const int motorL1 = 7;
const int motorL2 = 8;
const int motorLPWM = 6;

const int motorR1 = 12;
const int motorR2 = 13;
const int motorRPWM = 11;

//---------------------------------------
// Servo Loop Class
// A Proportional/Derivative feedback loop for pan/tilt servo tracking of blocks.
// (Based on Pixy CMUcam5 example code) //---------------------------------------
class ServoLoop
{ public:
ServoLoop(int32_t proportionalGain, int32_t derivativeGain);
void update(int32_t error);
int32_t m_pos;
int32_t m_prevError; 
int32_t m_proportionalGain; 
int32_t m_derivativeGain;
};

// ServoLoop Constructor
ServoLoop::ServoLoop(int32_t proportionalGain, int32_t derivativeGain) {
m_pos = RCS_CENTER_POS;
m_proportionalGain = proportionalGain;
m_derivativeGain = derivativeGain; 
m_prevError = 0x80000000L;
}
// ServoLoop Update
// Calculates new output based on the measured error and the current state.
void ServoLoop::update(int32_t error)
{
long int velocity;
char buf[32];
if (m_prevError!=0x80000000) {
  velocity = (error*m_proportionalGain + (error - m_prevError)*m_derivativeGain)>>10;
  m_pos += velocity;
  if (m_pos>RCS_MAX_POS) {
    m_pos = RCS_MAX_POS; 
  }
  else if (m_pos<RCS_MIN_POS) {
    m_pos = RCS_MIN_POS; 
  }
}
m_prevError = error; 
}
// End Servo Loop Class //---------------------------------------
Pixy pixy; // Declare the camera object
ServoLoop panLoop(200, 200); // Servo loop for pan 
ServoLoop tiltLoop(150, 200); // Servo loop for tilt

//ZumoMotors motors; // declare the motors on the zumo
//---------------------------------------
// Setup - runs once at startup 
//--------------------------------------- 

void setup()
{
Serial.begin(9600);
Serial.print("Starting...\n");
pixy.init();
}

uint32_t lastBlockTime = 0;
//---------------------------------------
// Main loop - runs continuously after setup //---------------------------------------
void loop()
{
uint16_t blocks;
blocks = pixy.getBlocks();
// If we have blocks in sight, track and follow them 
if (blocks){
  int trackedBlock = TrackBlock(blocks);
  FollowBlock(trackedBlock);
  lastBlockTime = millis();
}
else if (millis() - lastBlockTime > 100) {
  //motors.setLeftSpeed(0); //******
  //motors.setRightSpeed(0);
  digitalWrite(motorL1, HIGH);
  digitalWrite(motorL2, LOW);
  analogWrite(motorLPWM, 0);

  digitalWrite(motorL1, HIGH);
  digitalWrite(motorL2, LOW);
  analogWrite(motorLPWM, 0);
  ScanForBlocks();
} 
}

int oldX, oldY, oldSignature;
//---------------------------------------
// Track blocks via the Pixy pan/tilt mech
// (based in part on Pixy CMUcam5 pantilt example) //---------------------------------------
int TrackBlock(int blockCount)
{
int trackedBlock = 0;
long maxSize = 0;

Serial.print("blocks =");
Serial.println(blockCount);

for (int i = 0; i < blockCount; i++) {
  if ((oldSignature == 0) || (pixy.blocks[i].signature == oldSignature)) {
    long newSize = pixy.blocks[i].height * pixy.blocks[i].width;
    if (newSize > maxSize){
      trackedBlock = i;
      maxSize = newSize; 
    }
  }
}

int32_t panError = X_CENTER - pixy.blocks[trackedBlock].x; 
int32_t tiltError = pixy.blocks[trackedBlock].y - Y_CENTER;

panLoop.update(panError);
tiltLoop.update(tiltError);

pixy.setServos(panLoop.m_pos, tiltLoop.m_pos);

oldX = pixy.blocks[trackedBlock].x;
oldY = pixy.blocks[trackedBlock].y;
oldSignature = pixy.blocks[trackedBlock].signature;
return trackedBlock;
}

//---------------------------------------
// Follow blocks via the Zumo robot drive //
// This code makes the robot base turn
// and move to follow the pan/tilt tracking
// of the head. 
//--------------------------------------- 
int32_t size = 400;
void FollowBlock(int trackedBlock) {
int32_t followError = RCS_CENTER_POS - panLoop.m_pos; // How far off-center are we looking now?
// Size is the area of the object.
// We keep a running average of the last 8.
size += pixy.blocks[trackedBlock].width * pixy.blocks[trackedBlock].height; 
size -= size >> 3;

// Forward speed decreases as we approach the object (size is larger) 
int forwardSpeed = constrain(400 - (size/256), -100, 400);

// Steering differential is proportional to the error times the forward speed 
int32_t differential = (followError + (followError * forwardSpeed)) >> 8;

// Adjust the left and right speeds by the steering differential.
int leftSpeed = constrain(forwardSpeed + differential, -400, 400); 
int rightSpeed = constrain(forwardSpeed - differential, -400, 400);

// And set the motor speeds 
//motors.setLeftSpeed(leftSpeed); //******
//motors.setRightSpeed(rightSpeed);
digitalWrite(motorL1, HIGH);
digitalWrite(motorL2, LOW);
analogWrite(motorLPWM, leftSpeed);

digitalWrite(motorR1, HIGH);
digitalWrite(motorR2, LOW);
analogWrite(motorRPWM, rightSpeed);
}

//---------------------------------------
// Random search for blocks
//
// This code pans back and forth at random until a block is detected //---------------------------------------
int scanIncrement = (RCS_MAX_POS - RCS_MIN_POS) / 150;
uint32_t lastMove = 0;

void ScanForBlocks() {
if (millis() - lastMove > 20) {
  lastMove = millis();
  panLoop.m_pos += scanIncrement;
    if ((panLoop.m_pos >= RCS_MAX_POS)||(panLoop.m_pos <= RCS_MIN_POS)) {
      tiltLoop.m_pos = random(RCS_MAX_POS * 0.6, RCS_MAX_POS); 
      scanIncrement = -scanIncrement;
        if (scanIncrement < 0){
            //motors.setLeftSpeed(-250); //*****
            //motors.setRightSpeed(250);
            digitalWrite(motorL1, LOW);
            digitalWrite(motorL2, HIGH);
            analogWrite(motorLPWM, 200); 

            digitalWrite(motorR1, HIGH);
            digitalWrite(motorR2, LOW);
            analogWrite(motorRPWM, 200);
           }
        else {
            //motors.setLeftSpeed(+180);
            //motors.setRightSpeed(-180); 
            digitalWrite(motorL1, HIGH);
            digitalWrite(motorL2, LOW);
            analogWrite(motorLPWM, 200);

            digitalWrite(motorR1, LOW);
            digitalWrite(motorR2, HIGH);
            analogWrite(motorRPWM, 200);
            }
      delay(random(250, 500)); 
      }
  pixy.setServos(panLoop.m_pos, tiltLoop.m_pos);
  }
}

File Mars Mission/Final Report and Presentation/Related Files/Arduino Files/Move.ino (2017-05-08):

void left(int PWM) {
  int pin1 = LOW;
  int pin2 = LOW;
  
  if(PWM > 0) {
    pin1 = HIGH;
  } else if(PWM < 0){
    PWM = -PWM;
    pin2 = HIGH;
  }
  PWM = constrain(PWM, 0, 255);
  
  digitalWrite(motorL1, pin1);
  digitalWrite(motorL2, pin2);
  analogWrite(motorLPWM, PWM);
}

void right(int PWM) {
  int pin1 = LOW;
  int pin2 = LOW;
  
  if(PWM > 0) {
    pin1 = HIGH;
  } else if(PWM < 0){
    PWM = -PWM;
    pin2 = HIGH;
  }
  PWM = constrain(PWM, 0, 255);
  
  digitalWrite(motorR1, pin1);
  digitalWrite(motorR2, pin2);
  analogWrite(motorRPWM, PWM);
}

void moveMotor(int leftPWM, int rightPWM) {
  left(leftPWM);
  right(rightPWM);
}


void stopMove() {
  moveMotor(0, 0);
}

void breakMove() {
  digitalWrite(motorL1, LOW);
  digitalWrite(motorL2, LOW);
  analogWrite(motorLPWM, 255);
  
  digitalWrite(motorR1, LOW);
  digitalWrite(motorR2, LOW);
  analogWrite(motorRPWM, 255);

  delay(200);
  stopMove();
}


void FollowBlock(int trackedBlock) {
  int forwardSpeed = 140;
    
  // Steering differential is proportional to the off center value
  int differential = 160 - pixy.blocks[trackedBlock].x;
  
  // Adjust the left and right speeds by the steering differential.
  int leftSpeed = constrain(forwardSpeed - 0.8*differential, -SPEED, SPEED);
  int rightSpeed = constrain(forwardSpeed + 0.8*differential, -SPEED, SPEED);

  moveMotor(leftSpeed, rightSpeed);
}


void ScanForBlocks() {
  static uint32_t lastMove = 0L;
  static uint32_t lastStraight = 0L;
  static int forwardCount = 0;
  
  if (millis() - lastMove > 20) {
    int frontDist = analogRead(irFront);
    int rightDist = analogRead(irRight);
    lastMove = millis();
    

    if(rightDist > 500) {
      dir = LEFT;
    } else {
      if(dir == LEFT) {
        dir = FORWARD;
      } else if(millis() - lastStraight > 2000){
        {
          if(forwardCount < 10) {
            forwardCount++;
            dir = FORWARD;
          }
          else {
            dir = RIGHT;
            forwardCount = 0;
            lastStraight = millis();
          }
        }
      } else{
        dir = RIGHT;
      }
    }
     

    if(frontDist > 500) {
      dir = BACKWARD;
      forwardCount = 0; 
      lastStraight = millis();
    }
    switch(dir) {
      case FORWARD:
        moveMotor(160, 160);
        break;
      case LEFT:
        moveMotor(-100, 100);
        break;
      case RIGHT:
        moveMotor(100, -100);
        break;
      case BACKWARD:
        moveMotor(-200, -200);
        break;
    }
  }
  /*

  static uint32_t lastMove = 0L;
  int leftSpeed = 100;
  int rightSpeed = -100;
  
  if (millis() - lastMove > 20) {
    if(millis() - lastStraight > 3000) {
      lastStraight = millis();
      leftSpeed = 140;
      rightSpeed = 140;
    }
    
    lastMove = millis();

    if(getRightDistance() > 500) {
      //Right obstacle
      leftSpeed = -1;
      rightSpeed = 140;
      delay(100);
    }

    if(getFrontDistance() > 500) {
      //Front obstacle
      leftSpeed = -140;
      rightSpeed = -140;
      lastStraight = millis();
    }
    
    moveMotor(leftSpeed, rightSpeed);
  }
*/
}

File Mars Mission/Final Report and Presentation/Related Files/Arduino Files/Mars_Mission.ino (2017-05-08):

#include <SPI.h>
#include <Pixy.h>
#include <Servo.h>
#include <IRremote.h>


#define DEBUG true
#define TIMEOUT 40*1000
#define DELAY_DOOR 30
#define SERVO_CLOSE 100
#define SERVO_OPEN 0
#define SIGNATURE_BALL 1
#define SIGNATURE_CONTAINER 2
#define DEFAULT_BLOB_SIZE 200
#define MIN_BLOB_SIZE 10
#define SPEED 140

//All pins
const int motorL1 = 7;
const int motorL2 = 8;
const int motorLPWM = 6;

const int motorR1 = 12;
const int motorR2 = 13;
const int motorRPWM = 11;

const int switchF = 3;
const int switchR = 4;

const int irFront = 0;
const int irRight = 7;

const int interruptPin = 2;

bool started;

int blob_x;
int blob_y;
int blobSize;
bool foundBlob;
int ballCount;

bool doorClosed;
int trackedBlock;

enum State {
    BALL,
    COLLECT,
    CONTAINER,
    EMPTY,
    HALT
  } state;

enum Dir {
    FORWARD,
    LEFT,
    RIGHT,
    BACKWARD
} dir;


Servo doorservo;
Pixy pixy;
IRsend irsend;

void setup()
{
  
  if(DEBUG) {
    Serial.begin(9600);
    Serial.print("Initializing...\n");
  }
  pixy.init();
  doorservo.attach(10);
  
  pinMode(switchF, OUTPUT);
  pinMode(switchR, OUTPUT);
  pinMode(interruptPin, INPUT_PULLUP);
  attachInterrupt(digitalPinToInterrupt(interruptPin), eStop, FALLING);
  
  foundBlob = false;
  doorClosed = false;
  ballCount = 0;
  trackedBlock = -1;
  state = BALL;
  dir = FORWARD;
  
  closeDoor();
  pushIn();
  stopMove();
  stopPush();

  if(DEBUG)
    Serial.print("Ready\n");
}

void eStop() {
  state = HALT;
}

void loop()
{
  switch(state) {
    case BALL:
      findBall();
      break;

    case HALT:
      stopMove();
      break;
  
    case COLLECT:
      collectBall();
      break;
  
    case CONTAINER:
      findContainer();
      break;
  
    case EMPTY:
      empty();
      break;
  }
}
